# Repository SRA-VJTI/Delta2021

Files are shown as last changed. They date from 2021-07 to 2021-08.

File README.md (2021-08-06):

# Delta-Resources-2021

---

## Table of Contents
- [Introduction](#introduction)
- [Proposal](#proposal)
- [Design](#design)
- [Journey](#journey)
- [Algorithms](#algorithms)
- [Software used](#software-used)
- [Competition Snaps](#competition-snaps)
- [Products used](#products-used)
- [Results](#results)
- [Prizes and Achievements](#prizes-and-achievements)
- [Team - DNS](#team---dns)
- [Mentors](#mentors)
- [Organizations](#organizations)
- [References](#references)

## Introduction
 
 - The **7th Delta International Smart & Green Manufacturing Contest** is themed "Seeking Smart IIoT Talents" and offered three tracks: "Innovative Machines", "Smart Factory", or "Better Future Living".
 - Our **Team DNS** took up the **Smart Factory track**, we were expected to present realistic solutions or approaches with digitalization, IIoT, and big data management for optimized production processes, high-efficiency management & production, enhanced safety & reliability, quality improvement, energy savings, predictive diagnosis and maintenance, and green solutions.
 - The Contest is **hosted by** the Chinese Association of Automation **(CAA)** and sponsored by the Chinese Association of Automation, and the Industry and Information Industry Vocational Education Teaching Steering Committee **under the Ministry of Education**. It is an innovative technology competition for automation, smart manufacturing solutions and green technology applications organized by the **Delta Group**.

## Proposal
- Our Team DNS proposed the Pick Sort Place Bot
- So after researching on some trends and practices currently followed in the packaging industry, we noticed that there were shortcomings in case of:
  * Variable sized item packaging
  * Location based item packaging
  * Custom subscription box based packaging
- And we took to solving that with our [proposed idea](https://github.com/SRA-VJTI/Delta2021/blob/main/docs/proposal/delta2021090_PSP_Bot_Proposal.pdf)

## Design
The complete mechanical structure is designed in **Solidworks2021**. Dimensions, assemblies and sub-parts were finalised considering the following:
* Material Strength
* Stress, material and displacement analysis
* Material Availability

### Manufactured Product
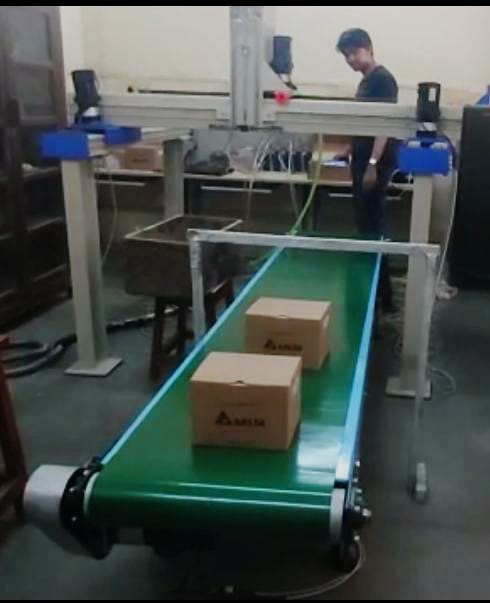
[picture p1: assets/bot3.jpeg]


### Raw Frame 
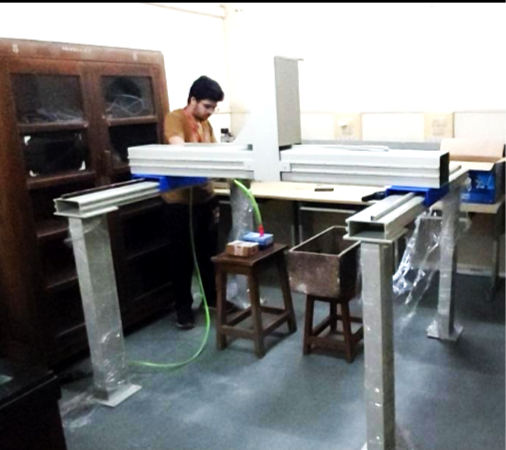
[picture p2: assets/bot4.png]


### Structure with Conveyor Setup
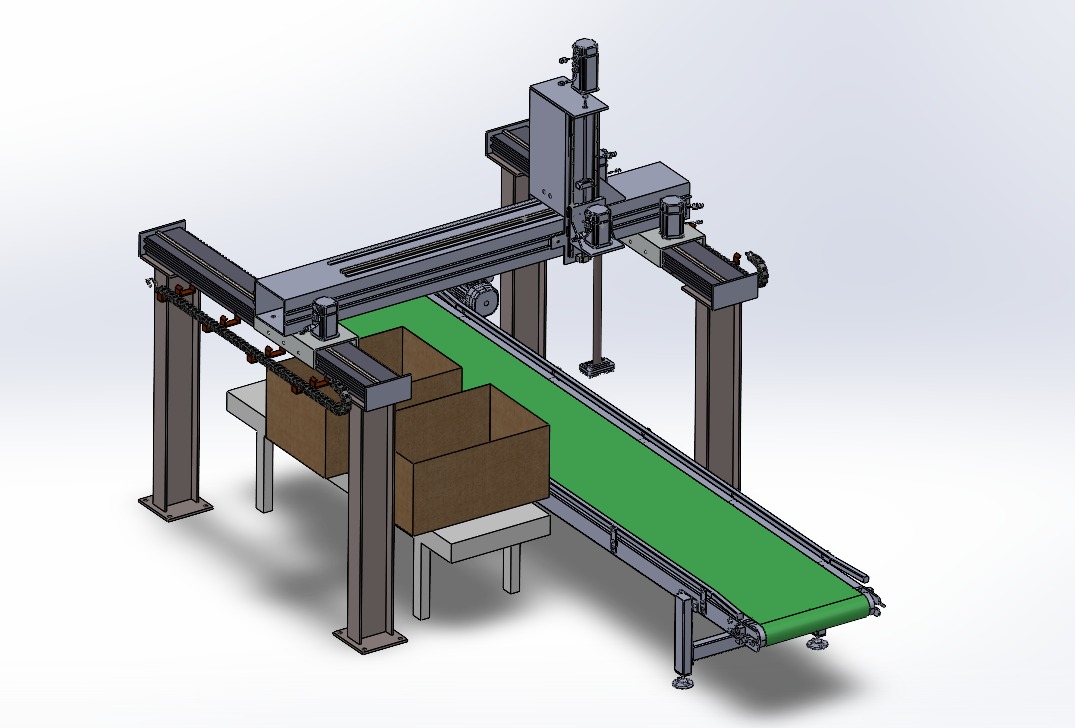
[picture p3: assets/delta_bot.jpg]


### XYZ Gantry Frame
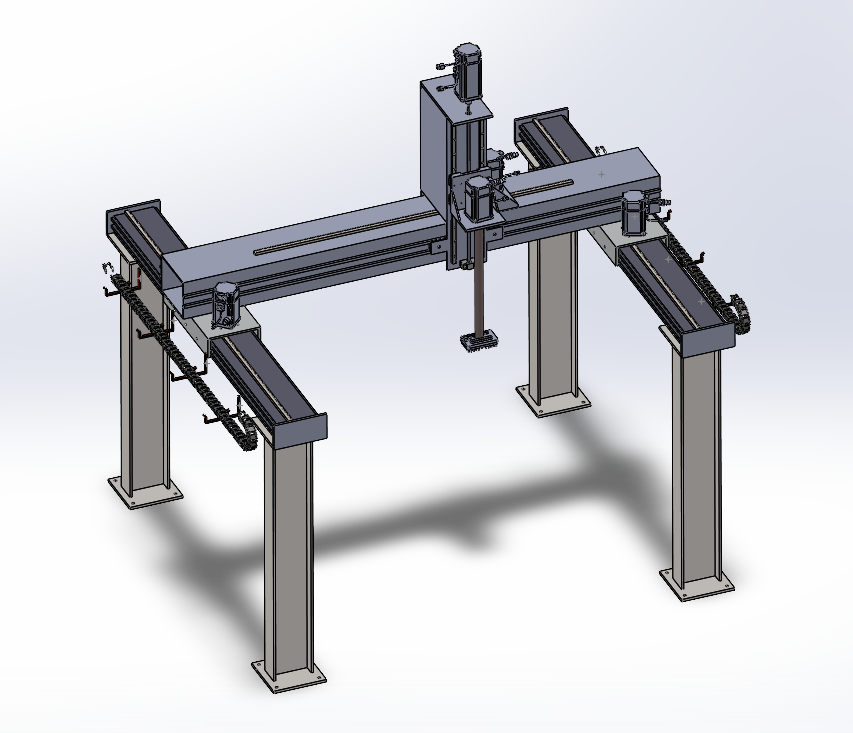
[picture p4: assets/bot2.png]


## Journey


## Algorithms
We are trying to implement a 3D binary packaging algorithm to reduce wastage of space ensuring efficient packaging of input items in output containers.
<table>
<tr>                   
<td>

### Loose Input Items
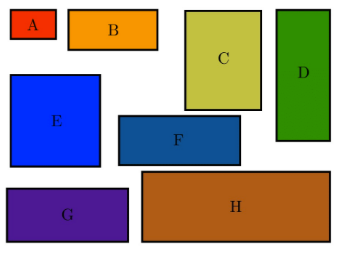
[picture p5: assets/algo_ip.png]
</tc>
<td>

### Close Packaging
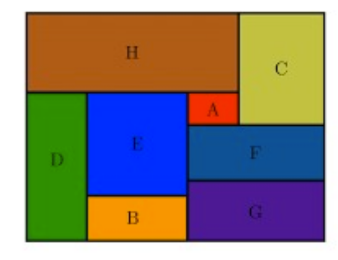
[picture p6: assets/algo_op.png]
</td>
</tr>
<tr>

### 3D Packaging
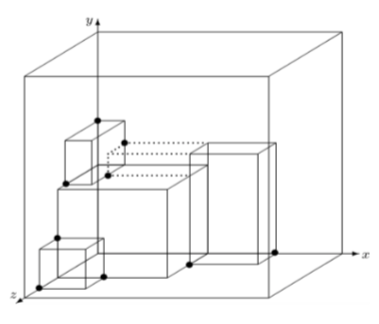
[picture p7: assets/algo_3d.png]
</tr>
</table>

## Software used
1. **Delta's CANopen** - To program the PLC Motion Controller. Currently, **ladder** language was used for programming.
2. **DOPsoft** - To design and program the Human Machine Interface - HMI.

## Competition Snaps
### X Y Axis Motion


## Products Used
### 1. PLC - Motion Controller 
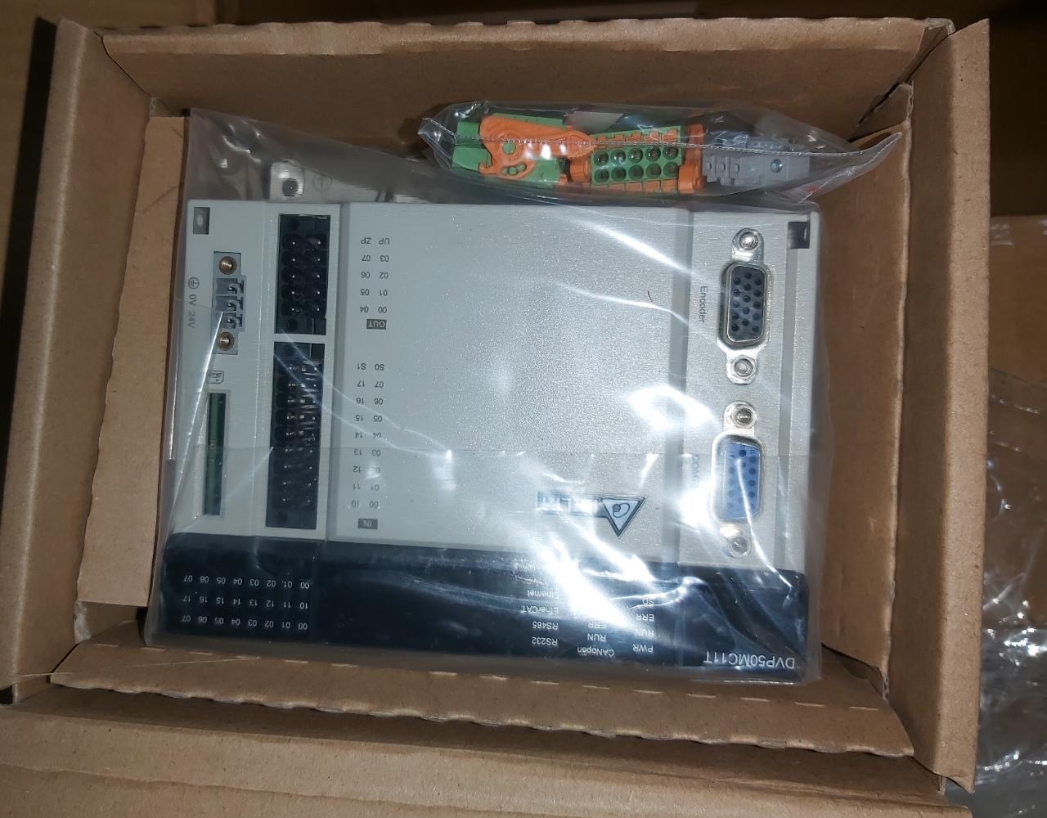
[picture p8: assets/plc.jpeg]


### 2. Conveyor Belt System
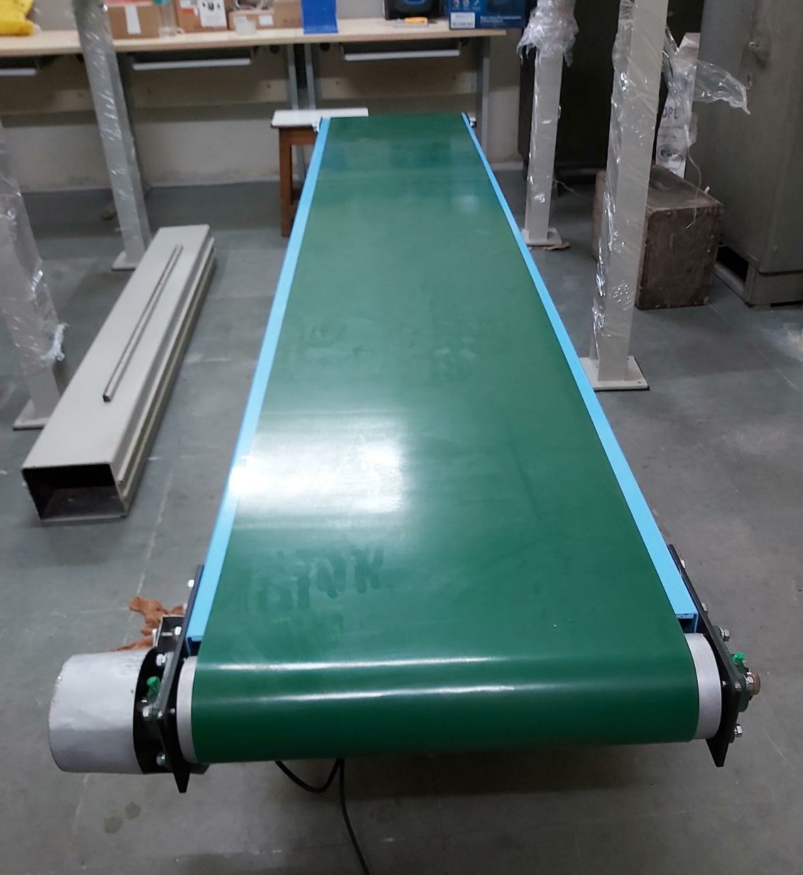
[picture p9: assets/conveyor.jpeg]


### 3. Machine Vision Lens and System
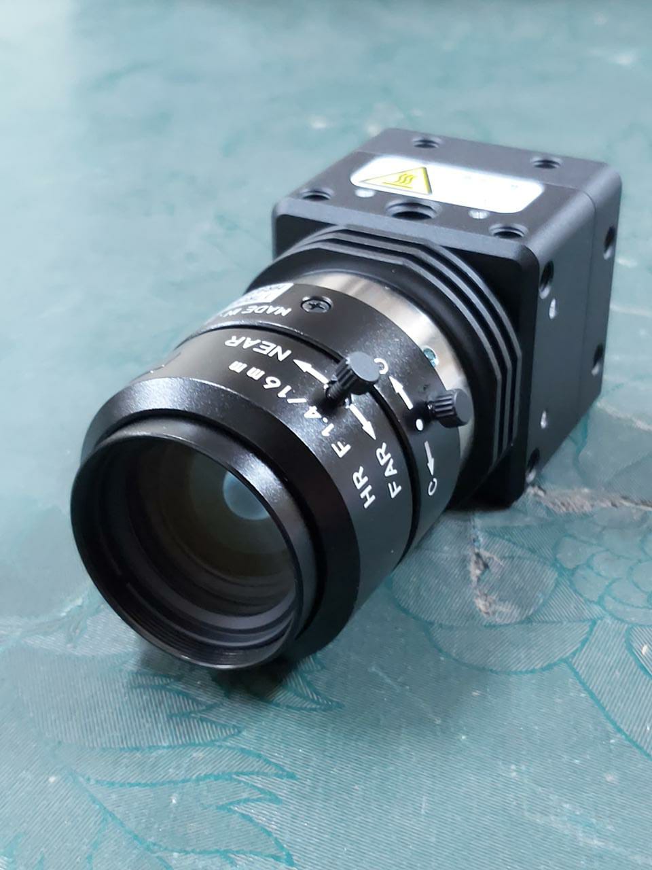
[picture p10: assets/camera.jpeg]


### 4. AC Servo Motor
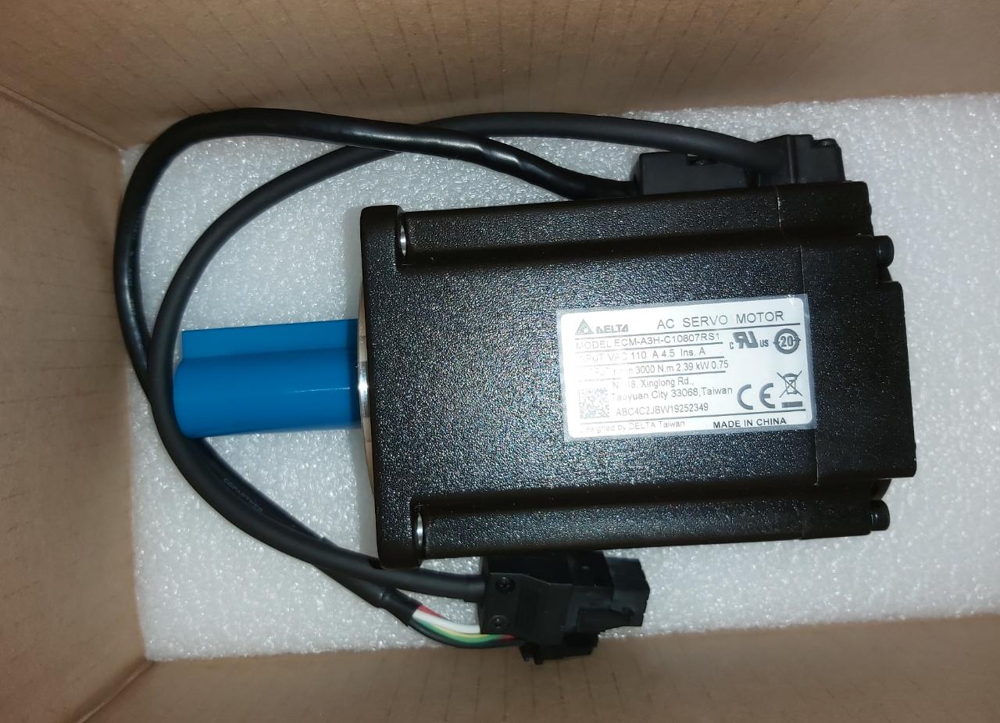
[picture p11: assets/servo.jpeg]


### 5. Servo Drives
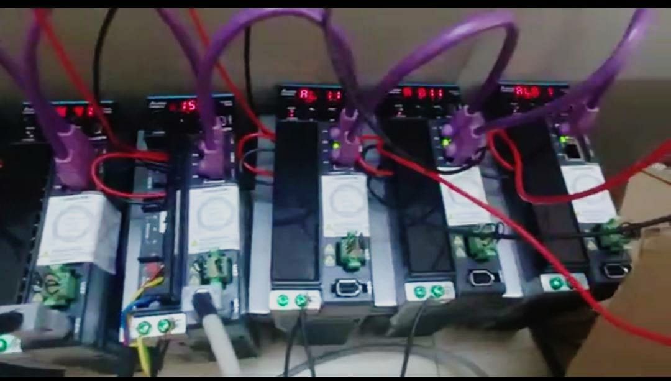
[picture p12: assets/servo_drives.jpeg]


### 6. IIoT Router
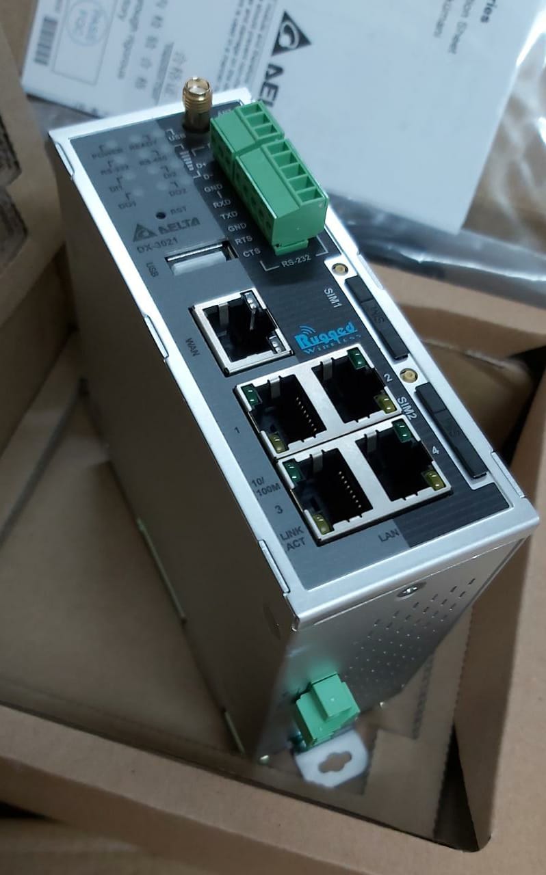
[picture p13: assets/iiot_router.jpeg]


### 7. HMI - Human Machine Interface
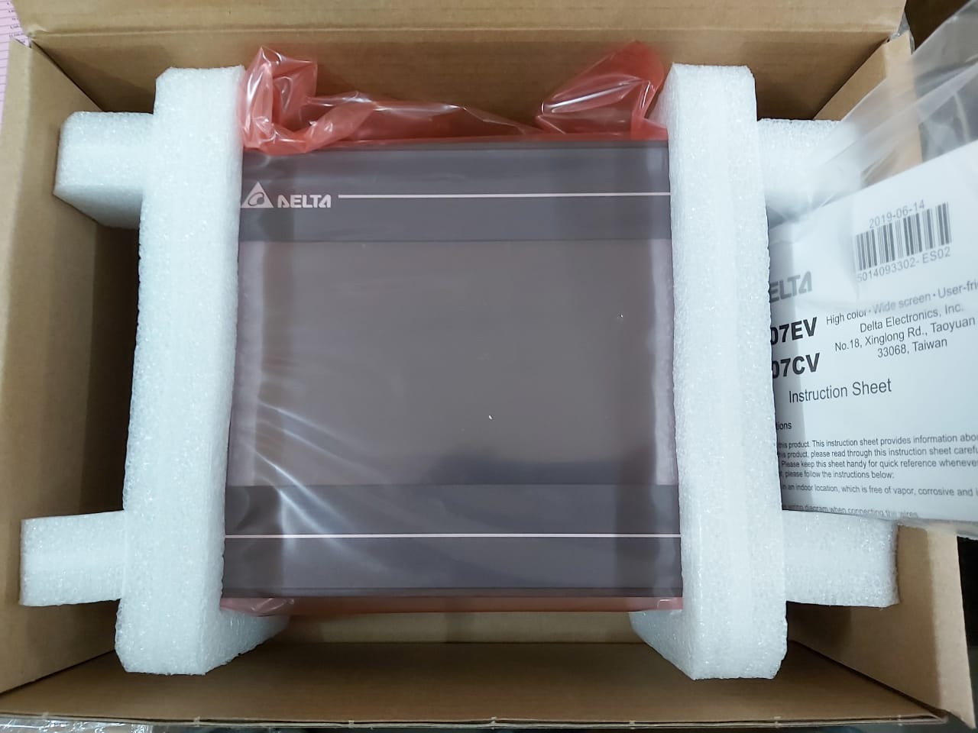
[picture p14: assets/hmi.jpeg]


### 8. Laser Displacement Sensor
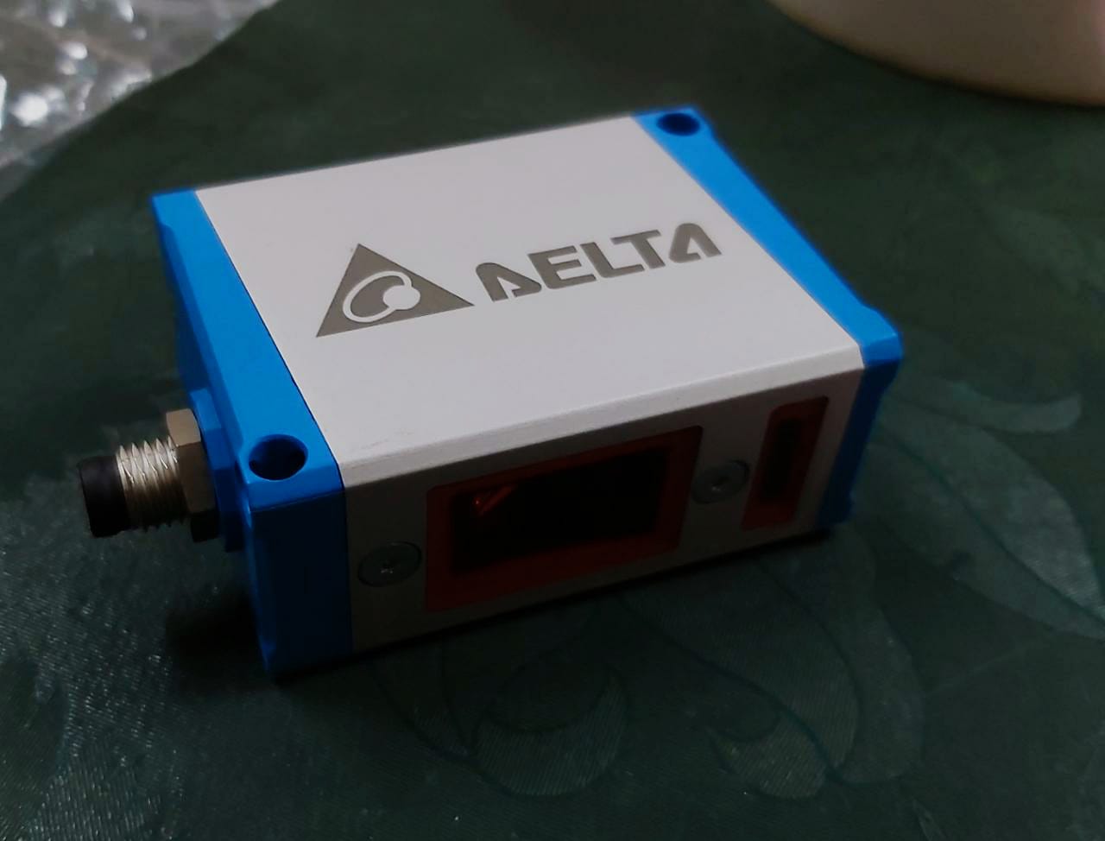
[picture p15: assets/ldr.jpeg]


## Results
- Representing India, Team DNS and VJTI bagged a rank under **Top 40** globally winning the **Second Prize** category.
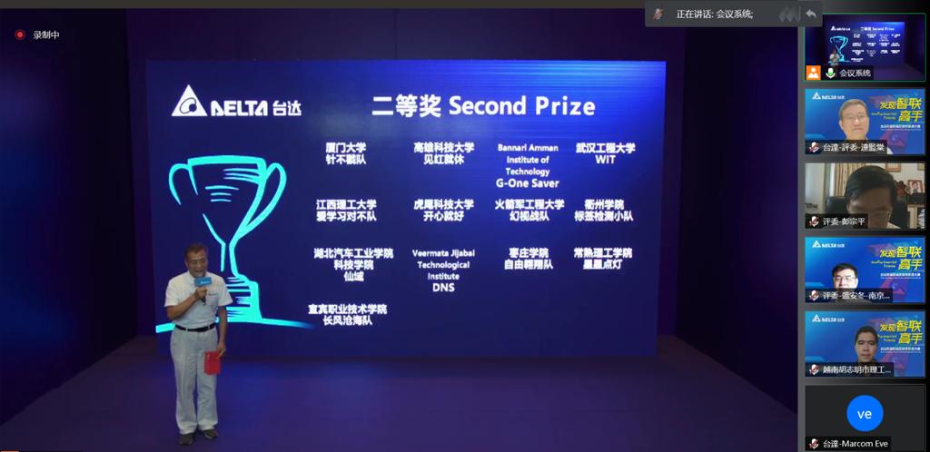
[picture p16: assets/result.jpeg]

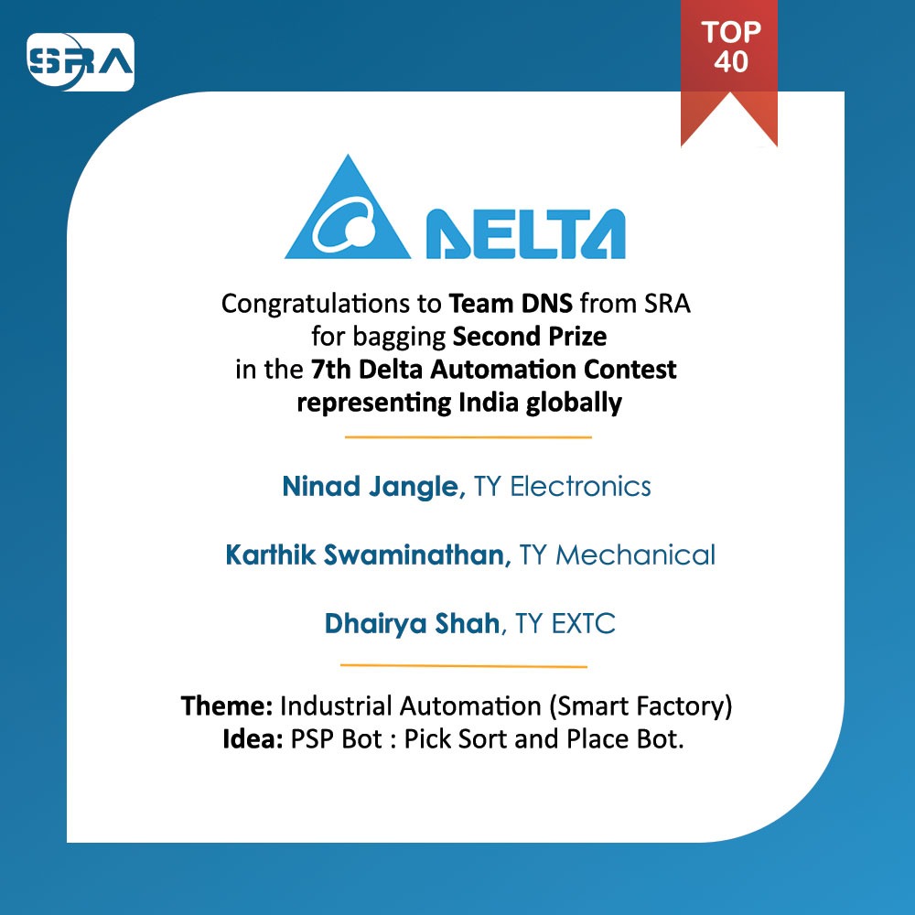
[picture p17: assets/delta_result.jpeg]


## Prizes and Achievements
1. Trophy Shield - Second Prize category
2. Delta's Industrial Automation Products Worth Rs 16.8 lakhs free of cost
3. 3000 RMB Cash Prize

## Team - DNS
- [Dhairya Shah](https://github.com/dhairyashah1/)
- [Karthik Swaminathan](https://github.com/kart1802/)
- [Ninad Jangle](https://github.com/ninja3011/)

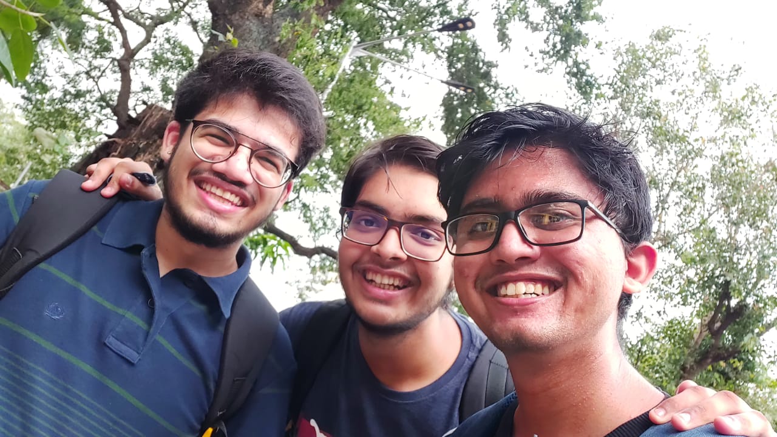
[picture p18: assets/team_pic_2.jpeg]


## Mentors
- [Dr. Faruk Kazi](https://www.linkedin.com/in/dr-faruk-kazi-vjti/?originalSubdomain=in)
- [Mr. Alister D'Silva](https://www.linkedin.com/in/alister-dsilva/)
- [Omkar Bhilare](https://www.linkedin.com/in/omkar-bhilare-985aa2180/)

## Organizations
- [VJTI](https://www.vjti.ac.in/)
- [SRA-VJTI](https://sravjti.in/)
- [COE-VJTI](https://www.vjti.ac.in/images/coe-cnds/project/index.html)
- [Absolute Motion Pvt Ltd](https://absolutemotion.in/)

## References

1. [Introductory Video](https://youtu.be/Td_gTH8elXg)
2. [Journey and Demo Video](https://youtu.be/JBdjbeT3EMY)
3. [Demo Video](https://youtu.be/Td_gTH8elXg)
4. [PSP BOT Presentation](https://github.com/SRA-VJTI/Delta2021/blob/main/docs/presentation/presentation.pdf)

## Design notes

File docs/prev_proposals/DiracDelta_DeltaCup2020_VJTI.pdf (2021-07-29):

## Seeking Smart Manufacturing Talents

## The 5th Delta Advanced Automation Contest

Project Proposal
Team Number:
Proposal Name | AARobot (Autonomous Agricultural Robot)
Team Name | Dirac Delta | University/ Affiliation | Veermata Jijabai Technological Institute, Mumbai, India
Team Leader | Name | Omkar Sargar | Department | B.Tech Electronics Engineering
| Mobile | 9969398226 | Post Code | 410206
| Email | omkarsargar01@gmail.com
| Address(City,State, Country) | 01, Nirman Sagar CHS, Thana Naka, Panvel, Maharashtra, India
Member Names | Lukesh Ankamwar B.Tech Electronics Engineering lukeshankamwar2103@gmail.com Omkar Bhilare B.Tech Electronics Engineering ombhilare999@gmail.com

## Team Building:

### 1. Mr. Omkar Shivaji Sargar (Age 19)

Bachelor of Technology Electronics Engineering, Veermata Jijabai Technological Institute (VJTI)
https://github.com/OSSome01
- Bachelor of Technology Electronics Engineering, 7.4 CGPA as on III semester (08/2018 to present) Maharashtra State Board Higher Secondary Certificate (Science), 78.45%

(08/2016 to 05/2018) All India Secondary Certificate Examination (10th Standard), 10/10 CGPA

(04/2015 to 04/2016)

Role: Computer Vision, Machine Learning and Programming.

Skills and Specialization: Hardware: NodeMCU, ESP-32, Rasberry Pi, Azure Sphere. Software Program: Eagle PCB, Multisim, ESP-IDF, Arduino IDE. Programming Languages: C, C++, Python, Robot Operating System (ROS),

Ladder Logic Programming, Data Structures and Algorithms. Key Technical Skills: Robotics, Simultaneous Localization And Mapping (SLAM),

Machine Learning, Computer Vision, Image Processing, Programming.

Specialization: Robotics and Automation.

Achievements: First prize: Labyrinth 2019 (Autonomous maze solving robot), VJTI. Third Prize: Autobot Challenge 2018, VJTI.

Projects: Smart Light: An IoT based project developed using ESP32, which optimizes the

brightness of an LED according to the ambient lighting conditions. Maze Solver: A robot designed to map any random maze in dry run and solve the maze

in the final run by following the shortest route possible. Object Detection: Software that uses a Kinect 360 to recognize a particular object in a

surrounding with the help of several digital image processing algorithms and provide the user with information like its distance from the camera, its dimensions and surface area. Self Balancing Robot based on PID controller: An Autonomous Robot that follows a

line and balances itself on only two wheels using PID control system and Embedded Electronics.

- 3-DOF Robotic Manipulator: A manipulator with 3 Degree of Freedom (DOF), interfaced with Robot Operating System (ROS) & implemented using ESP32. Simultaneous Localization And Mapping (SLAM): Simultaneous Automation

and Mapping using Intel Real Sense D435.

### 2. Mr. Omkar Ananda Bhilare (Age 19)

Bachelor of Technology Electronics Engineering, VeermataJijabai Technological Institute (VJTI)
https://www.linkedin.com/in/omkar-bhilare-985aa2180/ Bachelor of Technology Electronics Engineering, 9.73 CGPA as on III semester

(08/2018 to present) All India Secondary Certificate Examination(Diploma in Electronics), 97.15 %

(08/2016 to 05/2018) All India Secondary Certificate Examination (10th Standard), 95.2 % (04/2015

to 04/2016)

Role: Electronics and Electrical system design and programming.

Skills: Hardware: NodeMCU, Esp32, Atmel AVR(16,32,328P), Rasberry Pi. Software Program: MATLAB, Eagle PCB, Altium, Keil MDK, Multisim and

proteus Programming Languages: Embedded C, Python, C.

Specialization: Embedded System and Automation.

Achievements: State Rank 1 in electronics in diploma. Participated in various project presentation competition. Third Prize: Technical Paper Presentation, VJTI

Projects: Universal Integrated Circuit: The digital trainer kit which can clone multiple IC's Automated Seed Sower: Customizable robot which can sow seeds according to

user's need Line following robot. Home automation using NodeMCU Air quality monitoring system

### 3. Lukesh Narsingh Ankamwar (Age 20)

Bachelor of Technology Electronics Engineering, Veermata Jijabai Technological Institute (VJTI)
LinkedIn:-https://www.linkedin.com/in/lukesh-ankamwar-212566173/
- Bachelor of Technology Electronics Engineering, 8.13 CGPA as on III semester (08/2018 to present) Maharashtra State Board ,(12thStandard),83.33 % All India Secondary Certificate Examination (10th Standard), 90.4 %

Role: Mechanical system design and programming.

Skills: Hardware: NodeMCU, Esp32, Atmel AVR (16,32,328P), Rasberry Pi. Software Program: Solidworks, Crio, Ansys, MATLAB, Eagle PCB, Altium, Keil

MDK, Multisim and proteus Programming Languages: Python, C and C++.

Specialization: Mechanical Design and Analysis.

Achievements: First prize: Labyrinth 2019 (Autonomous maze solving robot), VJTI. Third Prize: Autobot Challenge 2018, VJTI.

Projects: Maze Solver: A robot designed to map any random maze in dry run and solve the maze

in the final run by following the shortest route possible. Object Detection: Software that uses a Kinect 360 to recognize a particular object in a

surrounding with the help of several digital image processing algorithms and provide the user with information like its distance from the camera, its dimensions and surface area. Self Balancing Robot based on PID controller: An Autonomous Robot that follows a

line and balances itself on only two wheels using PID control system and Embedded Electronics. 3-DOF Robotic Manipulator: A manipulator with 3 Degree of Freedom (DOF),

interfaced with Robot Operating System (ROS) & implemented using ESP32.

## Introduction:

Problem Insight:

Employment in the agricultural industry fell by 9 million from 2011 to 2018, contrasting to the 93 million increase in population in the same period. The newer generations are not interested in agriculture and hence the ratio of demand to supply is very high. Thus introducing automation and robotics in agriculture is a better method to improve overall agricultural produce and reduce labor requirements. There are very limited automatic agricultural robotic systems available in India but they are not feasible and are usually oriented towards harvesting, cleaning and packaging agricultural produce. The damage to agricultural crops due to pests account for 13.6% annual loss globally (which accounts for around 18 billion dollars). Similarly weeds amount to 8.8% annual loss globally. Additionally a loss of 861.8 million is incurred due to over usage of fertilizers in India. It would be a huge boon for the Indian Agricultural Industry if these losses can be minimized with the help of Automatic Agricultural Robots.
Project Idea:

After analysis the current situation of Automation in Agriculture we have come up with a innovative idea to design a solar powered agricultural robot which can do various tasks like: pest removal, weed removal, spraying fertilizer, helping in cattle farming, and generating electricity to power basic appliances in the farm. The robot will have two operating modes: automatic and semi-automatic. The robot will help to reduce the wastage of time and other resources needed in the above mentioned tasks. AARobot will also help to analyze the crops by sending data to a cloud server where analysis will be done on the data and the feedback will be provided to the farmers.
Using the concepts of Machine Learning, Computer Vision, Mobile Robotics we aim to build AARobot. Traditionally the main area of application of Automatic Agriculture Robots is at the harvesting stage. These robots are usually designed to do only a specific set of tasks, which makes them even more impractical for Indian farmers. We are aiming to maximize the produce by dealing with the losses incurred due to pests, weeds and overuse of fertilizers. Also we are designing a robot which can do varied tasks like helping in cattle farming, generating electricity for basic farm needs, and thus increasing its value for money.

## Objectives:

### 1. Crop Detection 2. Pest detection and removal 3. Weed detection and removal 4. Optimizing the process of spraying fertilizer 5. Analysis of data provided by AARobot. Sending all the data collected (Number of

crops, number of crops infected by pests, number of weeds detected, area of farm where maximum number of pests and weeds were detected, etc.) to a cloud and perform analysis on this data and give appropriate feedback to the farmer.
6. Designing a simple but effective system on the AARobot to help with cattle farming.
7. Charging a battery which can then be used for basic powering electrical appliances.

## Applications:

Crop Detection: We are using Machine Learning and Computer Vision algorithms to detect crops in the field. In our case we are detecting cabbage a common vegetable grown and consumed in India. After a plant is detected the robot will perform all the tests and the details of the plant will be uploaded on the cloud.

Case 1:
The damage caused to agricultural produce due to pests is very high. Traditional methods like using bright sticky pads are quite effective to counter flying pests; however there are no good solutions to counter bugs and ground pests. The only solution for bugs is the use of pesticides, but it leads to pollution and may also damage the crops if not used in proper quantities.
Solution:
Pest Detection and Removal: We are using Computer Vision algorithms to detect pests on cabbage plants. We are proposing to use a thermal camera which can be used to detect pests accurately. After a pest is detected a pest removal tool will help to suck off the pest from the plant. The detailed working of the pest removal tool is specified in the upcoming sections.

Case 2:
Traditionally weeds are removed manually by hand picking or by the use of weedicides. The first method impractical as it is very time consuming and is also not feasible as labor costs are very high. The second method leads to pollution and may destroy the crops if not used in proper quantities.
Solution:
Weed Detection and Removal: This will be similar to crop detection where Machine Learning and Computer Vision algorithms will be used. After a weed is detected a weed removal tool will act to remove the weed. The detailed working of the weed removal tool is specified in the upcoming sections.

Case 3:
Traditional methods of spraying fertilizer include manually spraying fertilizer using a pump like device. Manual spraying of fertilizers often lead to improper dosage to plants which may destroy the crops. It also leads to wastage of fertilizers. Manual spraying of fertilizers is also harmful for humans if proper precautions and safety measures are not followed. Solution:
Spraying Fertilizer: When a crop is detected the robot will calculate the midpoint of the crop and a spraying tool will spray the fertilizer at the exact location calculated, thus reducing the amount of fertilizer used and hence optimizing the process.

Case 4:
Usually in cattle farming when the cattle are to be taken out for grazing humans are needed to keep them in check and guide them to the grazing grounds.
Solution:
System for Cattle Farming: This is a simple add-on feature wherein a speaker can be mounted on the robot which will play the cattle owner’s voice in a loop to attract the cattle towards it. Thus it can be used to direct the cattle towards grazing grounds. It will help reduce the involvement of humans as the robot can be controlled remotely.

Case 5:
In India it is a common practice that in every farm there is a small room or house which is made to keep all the necessary tools and equipment (this room is equipped with basic electrical appliances like tube-light, fan, etc.). Also there are bore wells which are used as a primary water source for agriculture in many parts of India. Many regions in India don’t have electricity supply which makes it difficult for the farmers to use bore wells.
Solution:
Battery Charging: A additional feature which can be added is that AARobot can be used to charge a Battery which can then be used to power basic electrical appliances in the farm.

Use of IIoT: The contribution of agriculture plays an important role in the economic growth of

India. In India, more than 60% of peoples depend upon agriculture. This 60 % of people produce food for the country. Recently, the number of farmers in India decreasing day by day. The agriculture results depend up on the various controlled and uncontrolled factors like sudden change in climatic conditions; high and low rain fall and also the timing of the rain, storms and heat waves, and effects of cold, etc. For these conditions, traditional farming techniques are not appropriate. To minimize these effects and increase the productivity of agriculture,

automation and IoT techniques are required.

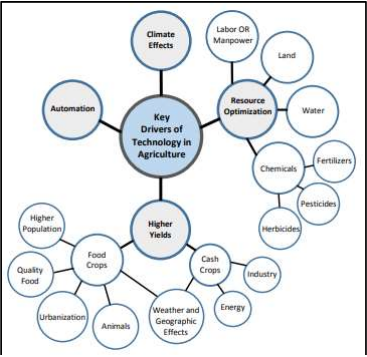
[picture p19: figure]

- In this project we have integrated internet of things such that the overall efficiency and usability Increases exponentially. We are focusing on automation of weed and pest removal and also, on resource optimization like chemicals, pesticides etc.

The use of IIOT in this project explained in following steps:

### 1. Detection of plant and its center:

- Before proceeding further for pest and weed removal we needed to detect plants, we have detected plant using OpenCV (computer vision). The example of detection of plant given below:

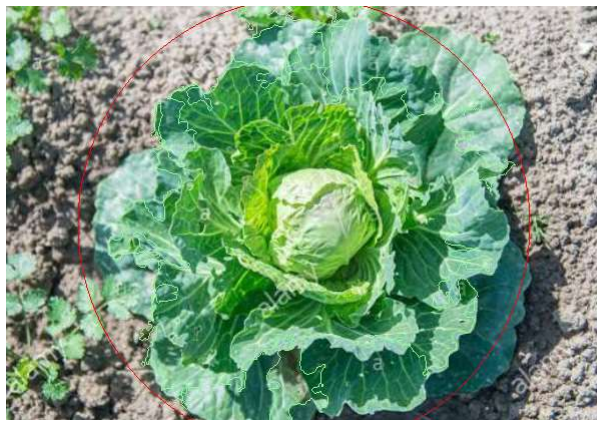
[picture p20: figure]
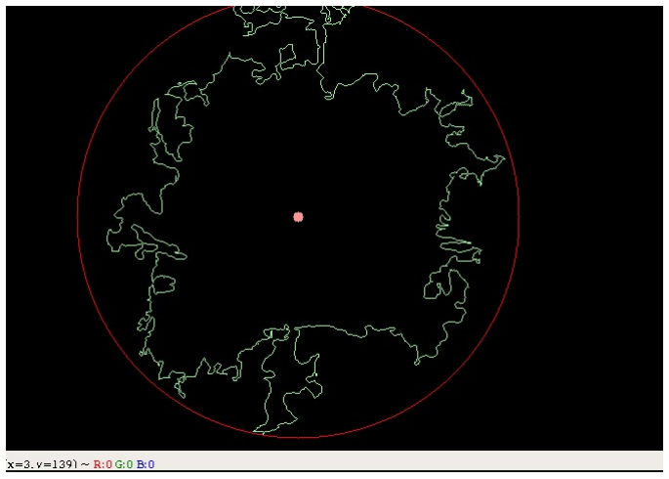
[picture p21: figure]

- By using OpenCV we were
which we can fertilize the plant, and if we provide the data set of same plant with infection.
- Then we can also detect
- And by using same technique we can also detect pest in plants and furth remove it using vacuum

### 2. Availability of data on cloud:

- After obtaining data from
further analyzing of obtained dat

CV we were able detect the center of the plant by using which we can fertilize the plant, and if we provide the data set of same

Infection in plant.
And by using same technique we can also detect pest in plants and furth vacuum

OpenCV program it is send to cloud for a

er

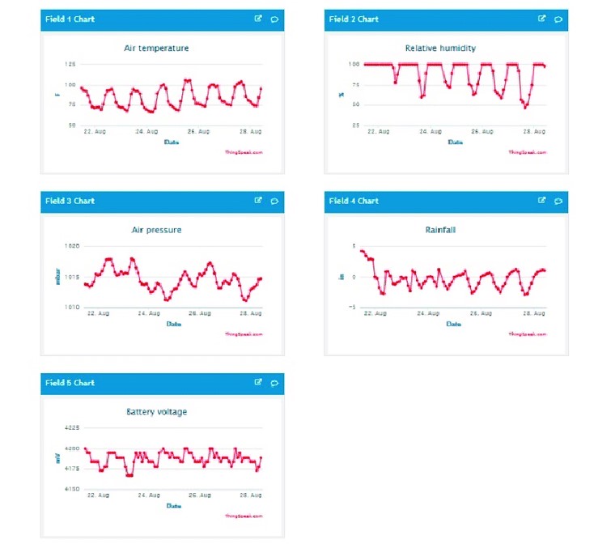
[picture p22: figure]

- We can monitor data on cloud and graphs like above can be made.
- In specific by plotting graph of pests captured w.r.t to its position in the field we can monitor the specific area where density of pests is more so one can take appropriate steps to reduce its adverse effects.

Thus, by using internet of things we can increase the productivity of agriculture and overall profit will also be increased because of IOT.

## Robot Design:

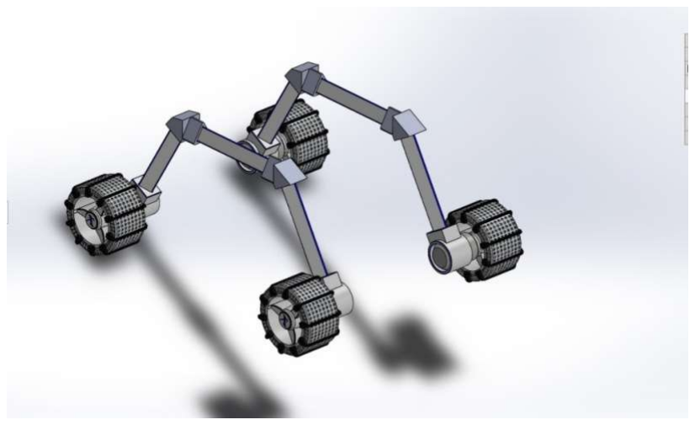
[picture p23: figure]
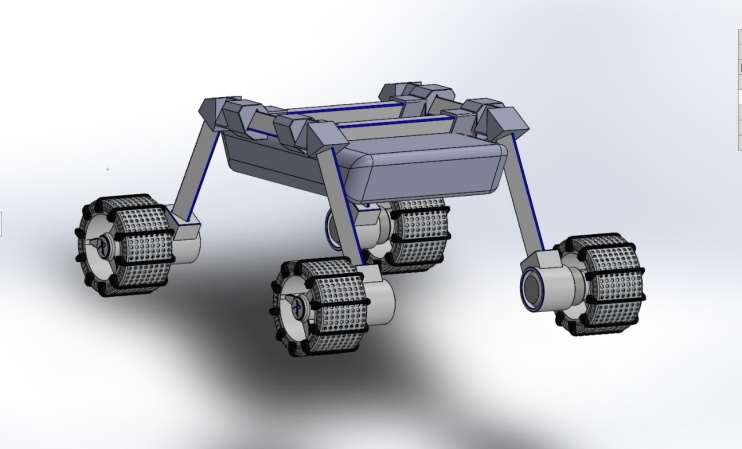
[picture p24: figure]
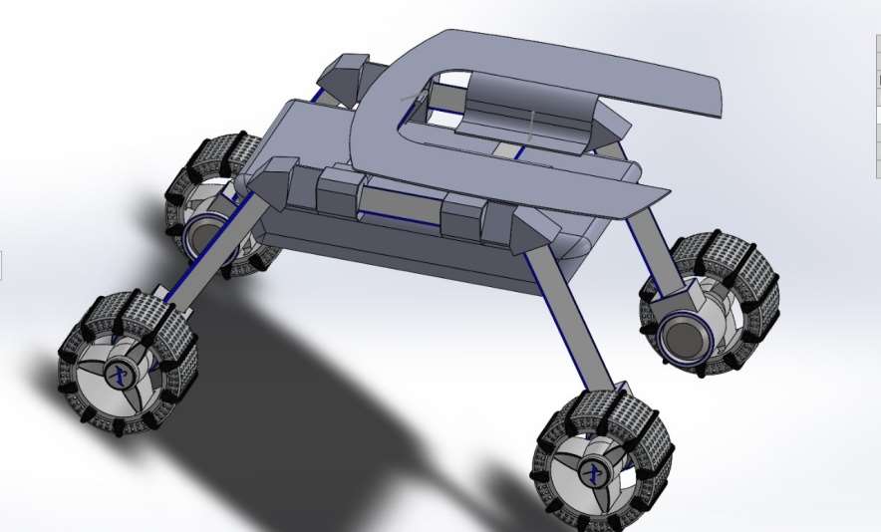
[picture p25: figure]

## Working:

Motion Control:

### 1. In the base of this project we are going to use two delta servo motor whic

coupled with the two rear wheels and front two wheels are used as dummy wheels.

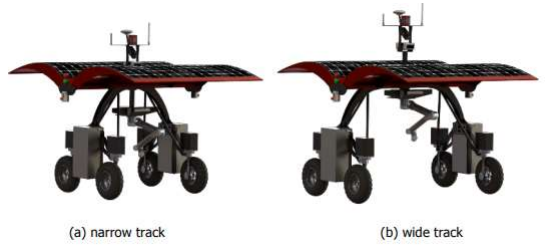
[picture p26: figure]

### 2. In this project, we are keeping wheel configuration dynamic that is the distance

between two side wheels can be customizable according to user input on HMI panel. T will be achieved by using two delta servo motors directly coupled to two lead screw.

3. In our project motion control system is going to have high accuracy, high speed, insignificant or no overshoot and robustness. To achieve this we are going to use a P controller which will be mathematical model of a motor based on classical root approach.

two delta servo motors directly coupled to two lead screw.

h are gear

his

ID
-locus

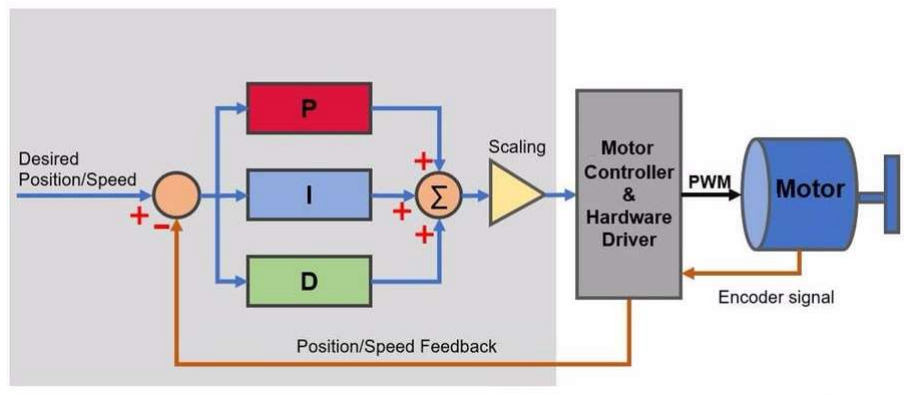
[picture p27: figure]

Tool Control:

In this Project we are using Three Main tools which are stated as below:

### 1. Vacuum for pest removal 2. Spray gun to spray fertilizers 3. Weed Removal tool for removing weed

1. Vacuum: A vacuum gun will be used to suck pests off the plants.
2. Spray gun: A pump motor is used to spray fertilizers on the farm land. Here we are using universal joint to move spray gun. The reason for using universal joint is to access every point in the frame.

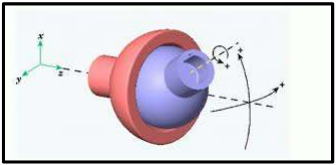
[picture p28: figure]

Working Video Link: https://youtu.be/Sef_fJh3OgQ

### 3. Weed Removal tool:

This robot can be also used to remove weeds from the surface of the field. To remove weed we have designed our own weed removal tool according to our need.

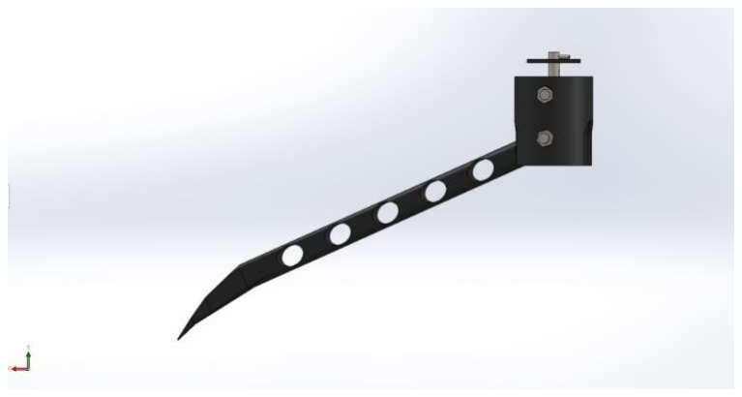
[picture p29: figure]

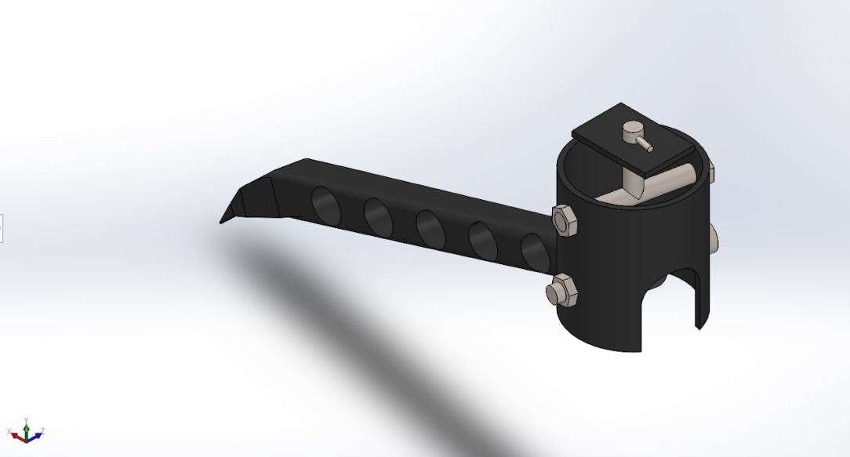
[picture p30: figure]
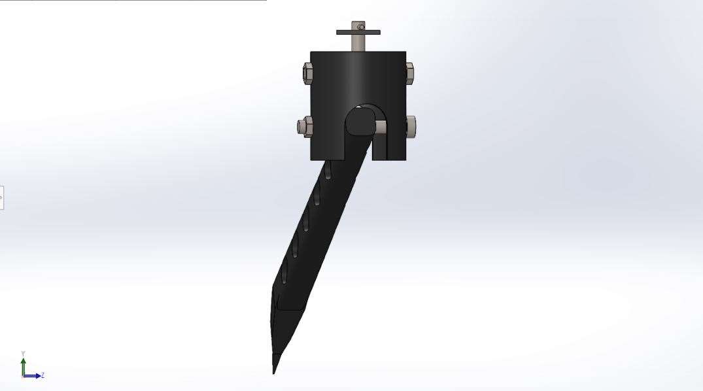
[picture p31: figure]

Working Video Link: https://youtu.be/WgTvQdC92Rchttps://youtu.be/4lKjg0JsSTg

Robot’s Work Space: Robot can move anywhere in the normal farm. Robot can move in muddy and rocky surface Cannot move on extremely uneven terrain.

Uncertain Error Handling: In any uncertain situation the robot will be stop working and battery will be open

Circuited so electrical safety is maintained. Emergency Alarm will be switched on and emergency light will be displayed HMI panel will show the information which will help to debug these uncertain errors.

## Innovative Planning and Value:

### 1. AARobot is a unique robot which will strive to increase the efficiency of tthe

agricultural industry. It is one of a kind robot which will help in such aspects of agriculture which are traditionally ignored by the other robots available in the industry.

### 2. The main idea is to make a multi-purpose automatic robot which can perform multiple

tasks and hence provide good value for money.

### 3. Using concepts like Machine Learning, Computer Vision and Mobile Robotics

AARobot will boost the agricultural industry and will help reduce human interference in agriculture.

## Cost Analysis, Feasibility and Reasonability:

As we are using all parts according to the industrial standards, we are having very cost-effective structure. AARobot is a multi-purpose robot and hence improves the value for money. If we compare the losses incurred by farmers due to the various issues which AARobot is trying to solve to the cost of the robot then we can say that its cost is well justified.

## Component Specification and Bill of Materials:

Sr | Product Name | Delta Product Code | Quantity | Description
1 | Wireless Module | DVW-W02W2-E2 | 2 | To connect with internet
2 | Servo Drivers | ASDA2ServoDrives | 4 | To drive all Axes motors
3 | Servo Motors with encoders | ASDA20721U | 4 | To drive all Axes motors
4 Planetary | Gearbox | PS Series | 2 | To change torque based on requirement for Constant speed motor.
5 | PLC | DVP28SV11R2 | 1 | Main controller which accept the input through HMI and cloud server and do control according to ladder logic.
6 | HMI | DOP-107WV | 1 | To observe the status of the robot on the field and to control it

7 AC-DC Power | Module | AB60S2400A | 1 | For power supply to PLC (24V)
8 Analog I/O | Modules | AH04AD-5A | 3
9 | Vision Sensor | VIS100 Series | 2 | For object detection on plants and positioning of robot

OTHER PRODUCTS

10 | Microprocessor | Raspberry Pi | 2 | For any alien object detection on plant and sensor data acquisition
11 | Wheels | Third Party | 4 | For moving the robot on field
12 BLDC Blower | Fan | Third Party | 2 | For cooling Drives
13 Power | Supply(5V) | Third Party | 2 | For powering microcontrollers and other peripherals
14 | Wire | Third Party | Multiple | Wiring
15 | Wire Connector | Third Party | Multiple | Wiring

16 | Microcontroller | Arduino UNO | 1 | For sensor data acquisition in BOTs
17 Ethernet Shield | for Arduino | Third Party | 1 | For IoT Application
18 Ball | Bearings | Third Party | Multiple | Miscellaneous
19 Linear | Bearings | Third Party | Multiple | Miscellaneous
20 | Solar Panels | Third Party | 2 | For charging the battery
21 | Nuts and Bots | Third Party | Multiple | Miscellaneous
22 Spacers and | Washers | Third Party | Multiple | Miscellaneous
23 | Power inverter | Third Party | 1 | For Solar Panel
24 | Kill Switch | Third Party | 1 | For Stopping all applications
25 | Sprinkler | Third Party | 2 | For sprinkling fertilisers
26 | Storage Tank | Third Party | 1 | For storing seeds/fertiliser
27 | Vacuum Pump | Third Party | 1
28 | DC Servos | Third Party | 5 | For use in various tools

## Future Scope:

1. It can be further used in Harvest management.
2. It can be also used for Field Mapping.
3. It can be used for Soil Management.
4. It can be an important part of a greener future for mass scale farming.
5. By bringing Artificial Intelligence and around the clock activity, the robots will help optimize the yield of farm far beyond what could humanly be possible.

## Summary:

The AARobot is thus a feasible multi-purpose automatic agricultural robot which can help boost the agricultural industry in India.

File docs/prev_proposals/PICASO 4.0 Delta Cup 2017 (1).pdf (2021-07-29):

## Seeking Smart Machine Talents

## The 4th Delta Advanced Automation Contest

## PROJECT PROPOSAL

TEAM Code: delta2017127 | TEAM ID: 435
Proposal Name | PICASO 4.0
Name Team | PICASO | University | Lovely Professional University, Punjab, India
Team Leader | Name | Mr. Arnab Kumar Das | Department | Bachelor of Technology Electronics and Communication
| Mobile | +91 9501991556 | Post Code | 713101
| Email | arnab.das.bwn@gmail.com
| Address | 56, Goal Ghar Saradapally, Near Goal Ghar Primary School, Burdwan, PIN – 713101, West Bengal, India
Member Names | Mr. Nikhil Goyal, B.Tech Electronics and Communication Engineering, nikhilgoyal2311@gmail.com , +91 9915727112 Mr. Veluguri Vinod, B.Tech Mechanical Engineering, vinod.veluguri@gmail.com , +91 9872386996

Team Building

### 1. Mr. Arnab Kumar Das, Age 23

Bachelor of Technology Electronics and Communication Engineering, Lovely Professional University
https://www.linkedin.com/in/arnabdasbwn/
Specialization: Embedded System and Robotics

ROAL: Electronics and Electrical System Design and Programming.

- Bachelor of Technology (Honors) Electronics and Communication Engineering, 9.0 CGPA as on VII Semester (08/2013 to Present)
- Indian School Certificate (12th Standard), 90.0% Aggregate Result (04/2011 to 04/2013)
- Indian Certificate Secondary Education (10th Standard), 87.8% Aggregate Result (04/2011)
- Hardware: Atmel AVR (16/32/328p), Raspberry Pi, Arduino, Microchip PIC, ARM7
- Software Program: AVR Atmel Studio, LabVIEW, Cadence, Eagle PCB, MATLAB, Keil MDK for ARM
- Programming Languages: Embedded C, Verilog, Embedded C++, Virtual Instrumentation, C, C++
- First Prize - Line Follower Robot Competition, Fluxus’16, IIT Indore, 2016
- Participated in Remote Control Ship and Aeroplane Competition, Cognizance’16, IIT Roorkee, 2016
- First Prize - Remote Control Car Race, Lovely Professional University, 2015
- Participated in E–Bike Manufacturing and Racing Challenge, Imperial Society of Innovative Engineers, 2015
- Participated in Hybrid Go-Kart Making Challenge, Imperial Society of Innovative Engineers, 2015
- Participated in World Skill India in Electronics, World Skill International Competition, 2015

### 2. Nikhil Goyal, Age 21

Bachelor of Tech Electronics and Communication Engineering, Lovely Professional University
https://www.linkedin.com/in/nikhil-goyal
Specialization: Automation and PLC

Role: PLC and HMI Programming

- Bachelor of Technology Electronics and Communication Engineering, 9.53 CGPA as on VII Semester (08/2013 to Present)

- Senior Secondary School (12th Standard), 87% Aggregate marks, (June 2013)
- Matriculation Examination (10th Standard), 85% Aggregate Result (June 2011)
- Software Program: Rockwell Automation, Factory Talk View ME, MATLAB, Proteus, Keil
- Programming Languages: PLC Programming, Verilog, Embedded C, C, C++, SQL, Java, Data Structure
- Hardware: Rockwell PLC, HMI, SCADA, Atmel AVR Microcontroller (16/32), 8051 Microcontroller
- Training on Automation, PLC, SCADA from Prudent Solutions WLL, Bahrain,2016
- Participated in Haptic Arm Robot Competition, Lovely Professional University, 2016
- Participated in IndoUs League Competition, Lovely Professional University, 2015
- Participated in Robotryst Competition, Lovely Professional University, 2015

### 3. Mr. Veluguri Vinod, Age 20

Bachelor of Technology Mechanical Engineering, Lovely professional University https://grabcad.com/vinod.sunny-1
Specialization: CAD Design and Optimization

ROAL: Designing and Manufacturing of The PICASO 4.0

- Bachelor of Technology Mechanical Engineering, 8.1 CPGA as on V Semester (08/2014 to Present)
- State Board Certificate (12th Standard), 89.7% Aggregate Result (06/2012 to 03/2014)
- State Board Certification of Secondary Education (10th Standard), 9.3 CGPA (03/2012)
- Software Program: AutoCAD, Catia V5, SolidWorks, Ansys Workbench, Ansys APDL
- Programming Language: C, C++, HTML
- Hardware: Lath Machine, Milling, Computer Numerical Control, Shaper, 8051 Microcontroller
- Certified SOLIDWORKS Professional-Core by Dassault systems ID:C-W68QFSKGGM on 8/Jan/2016
- Training on Computational Fluid Dynamics, Technosoft Educational and Research Consultancy, Delhi, 2016
- Participated in Indo Asian Solar Challenge, Lovely Professional University
- Certified Catia, Autocad and Ansys APDL, Workbench(structural) by Canter Cadd,2016
- Certified by Trinity College of London in English, Grade -9, 2010
- Participated in Hybrid Vehicle Challenge, Lovely Professional University
- Participated in E Bike Manufacturing Competition, Lovely Professional University

## Motivation and Design Concept:

Problem Insight:

If we see present painting industry, we find most of the painting are done manually using human labor. This includes house wall painting, sign board painting, advertisement painting, graffiti, line drawings etc. Manual painting is time consuming with low throughput and high cost of labor. Sometimes, it is difficult to meet the requirement of customers because of lack of painting skills. User has to be in touch with company for regular updates. Interaction with company is tedious and industry fails to fulfill customer satisfaction.

Project Idea:

Using the concept of Industry 4.0 and Made in China 2025 satisfying Smart Machine, Smart Robotics and Smart Manufacturing for a cost effective solution for paint industry that will increase productivity, limit human intervention, avoid physical hazard and maximize the output in limited time. We propose PICASO 4.0 a Delta DIA Cloud connected Computer Numeric Control (CNC) machine based Multi-Axes Motion Control robot for Automated Vertical Painting and Vertical Laser Engraving/Cutting solution for brick walls, concrete, glass, wood etc. or any vertical plane surface that can accept paint or laser.

We have successfully developed a CNC Drawing Robot (Picture Below) based on microcontroller and stepper motor with belt driven axis and we have got drawing with precision of 0.1mm. However, the system draws/writes using pen on paper placed horizontally and has a work area of 45cmX39cm. This became the motivation for PICASO 4.0.

WORKING VIDEO LINK OF OUR CNC DRAWING ROBOT (PLEASE WATCH)

https://www.youtube.com/watch?v=77SKv8xWuLk

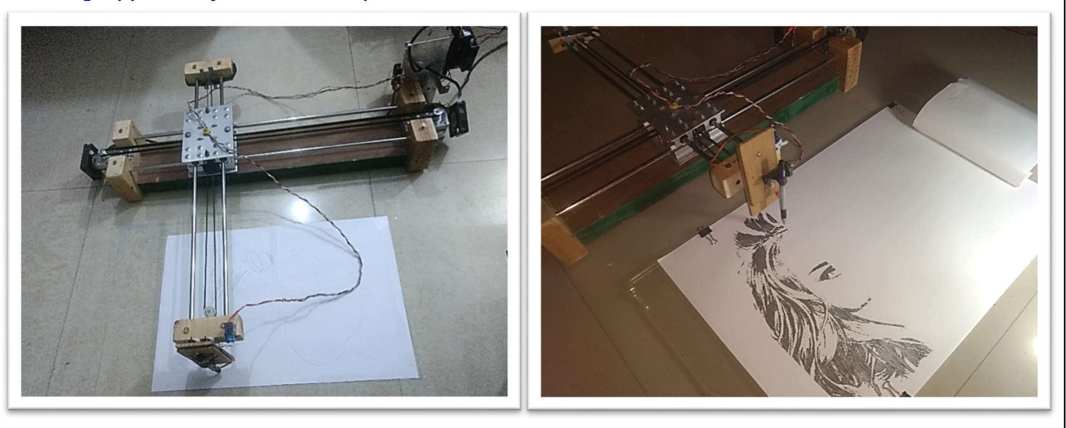
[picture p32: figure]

Fig 1: CNC drawing robot with paper | Fig 2: Drawing in raster printing mode

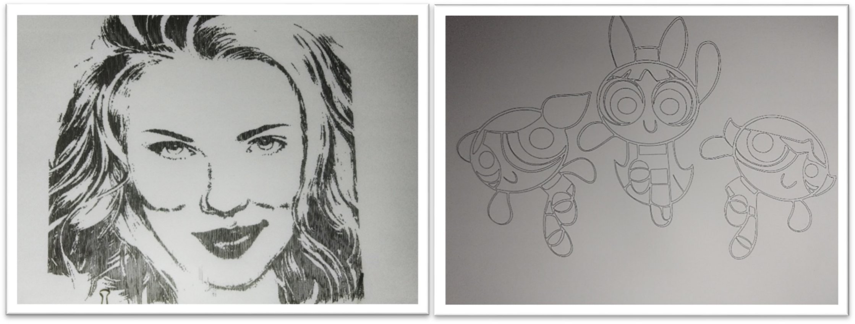
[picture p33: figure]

Fig 3: Raster printing output | Fig 4: Vector printing output

We have improved this idea to make a CNC based vertical painting/engraving/cutting robot placed parallel to a brick wall, concrete, glass wall, wood etc. which is capable of vertical painting/laser engraving customized drawing uploaded by the user on the cloud server. The system will have two tools a painting mechanism and a laser engraving We can paint walls as well as laser engrave vertical brick walls, concrete, glass, wood etc. and an extended application will be vertical laser cutting of wood or MDF.

## Objectives/Outcome:

Automate the painting process.
Increase precision in wall painting/engraving/cutting.
Vertical laser engraving/cutting and vertical painting in single machine. Increase productivity compared to manual painting.
Maximize profit in printing industry.
Reduce intake of toxic fumes from paint as only robot is involved in painting. Can work in high rise buildings where safety is a concern.
Remote monitoring of painting/engraving process through cloud.
Reduce manpower and human resource.

## Applications:

Case 1:

Customer Requirement:
A customer wants the wall of his house to be painted with his own customized design.

Solution:
Customer uploads the design to the cloud server, brings PICASO 4.0, aligns its painting tool towards wall, put it into painting mode, set painting area and enjoy the output.

Case 2:

Customer Requirement:
A customer has a glass door at his office entrance and he wants his company’s logo to be engraved on it but he does not want to invest in a new door and also he wants to avoid disassembly and reassembly of door.

Solution:
Bring PICASO 4.0, align its laser tool towards glass door, upload company’s logo to cloud server, put it into laser engraving mode, set engraving area and enjoy the output.

Case 3:

Customer Requirement
A customer has a large factory that has a concrete wall around its perimeter. Customer wants his perimeter to be painted with least labor cost and minimum time.

Solution:
Configure PICASO 4.0 to move around the perimeter wall and paint.

## Robot Design:

Our system is divided into three axes (X, Y, Z). The design consists of a base chassis on which the whole system stands. The base chassis houses all the servo drives, power supply, PLC, wiring, servo motors, etc. The base chassis has four servo motors that are attached with gear box, which are further attached with wheels. The chassis along with the wheels and servo forms the X axis. The X axis moves horizontally parallel to wall or work surface. Above the chassis runs vertically four aluminum extrusion which supports the Y axis for the system. The Y axis moves vertically up or down using two lead screw with two split nuts attached to the base of a sliding rack. The lead screws are rotated by servo motors coupled to it and are placed inside the chassis. The Z axis is above the rack of Y axis and moves two tools toward or away from the wall. We can place the robot in two orientations: one with printing head towards wall for printing and other one is laser towards wall for engraving. An HMI is attached to the side of the robot for real time monitoring, start, stop, emergency stop, etc.

PICASO 4.0 PRODUCT DESIGN ANIMATION :: https://youtu.be/C1ulfhZpyTI

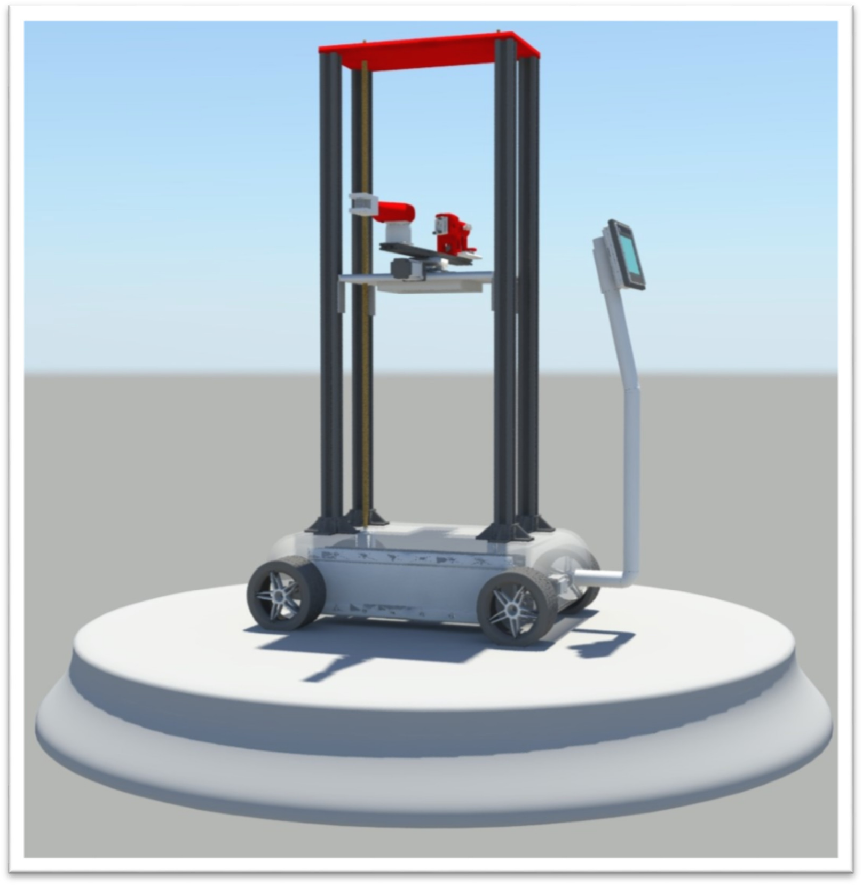
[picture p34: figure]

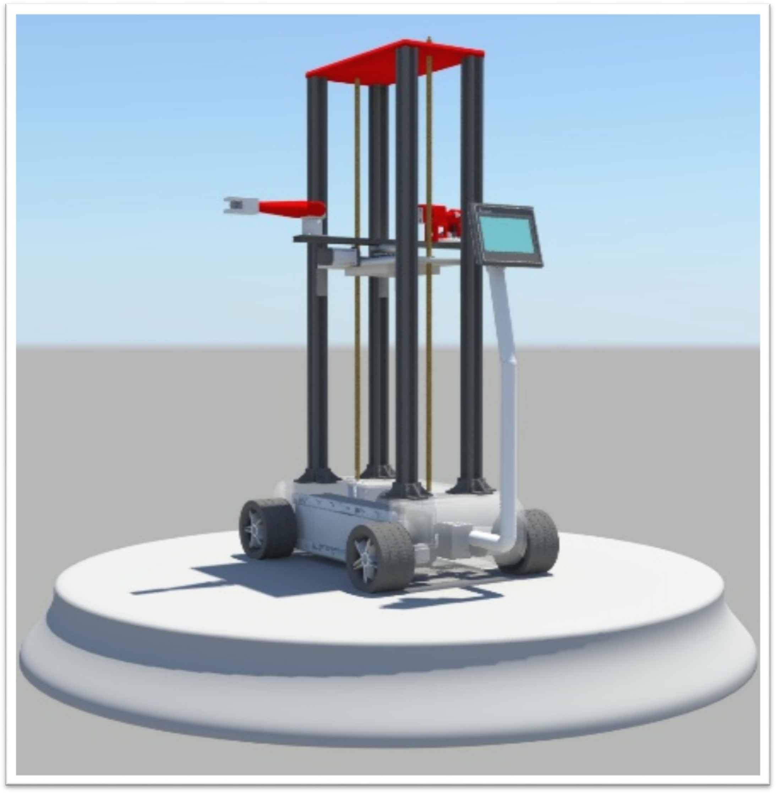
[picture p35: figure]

Fig: Isometric View with all assembly

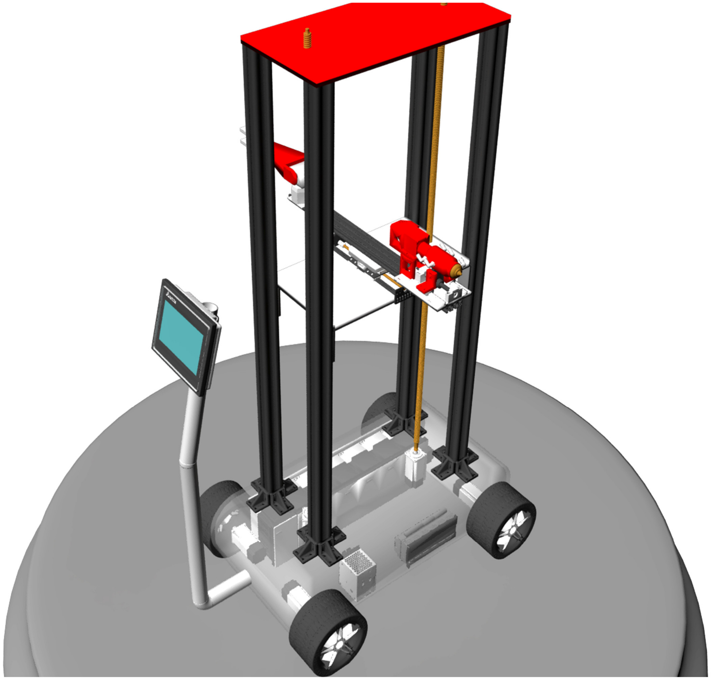
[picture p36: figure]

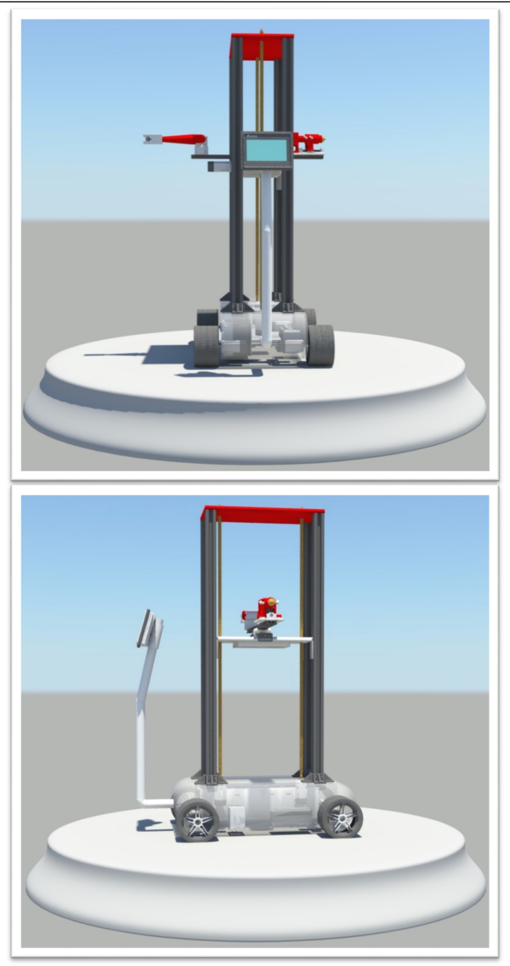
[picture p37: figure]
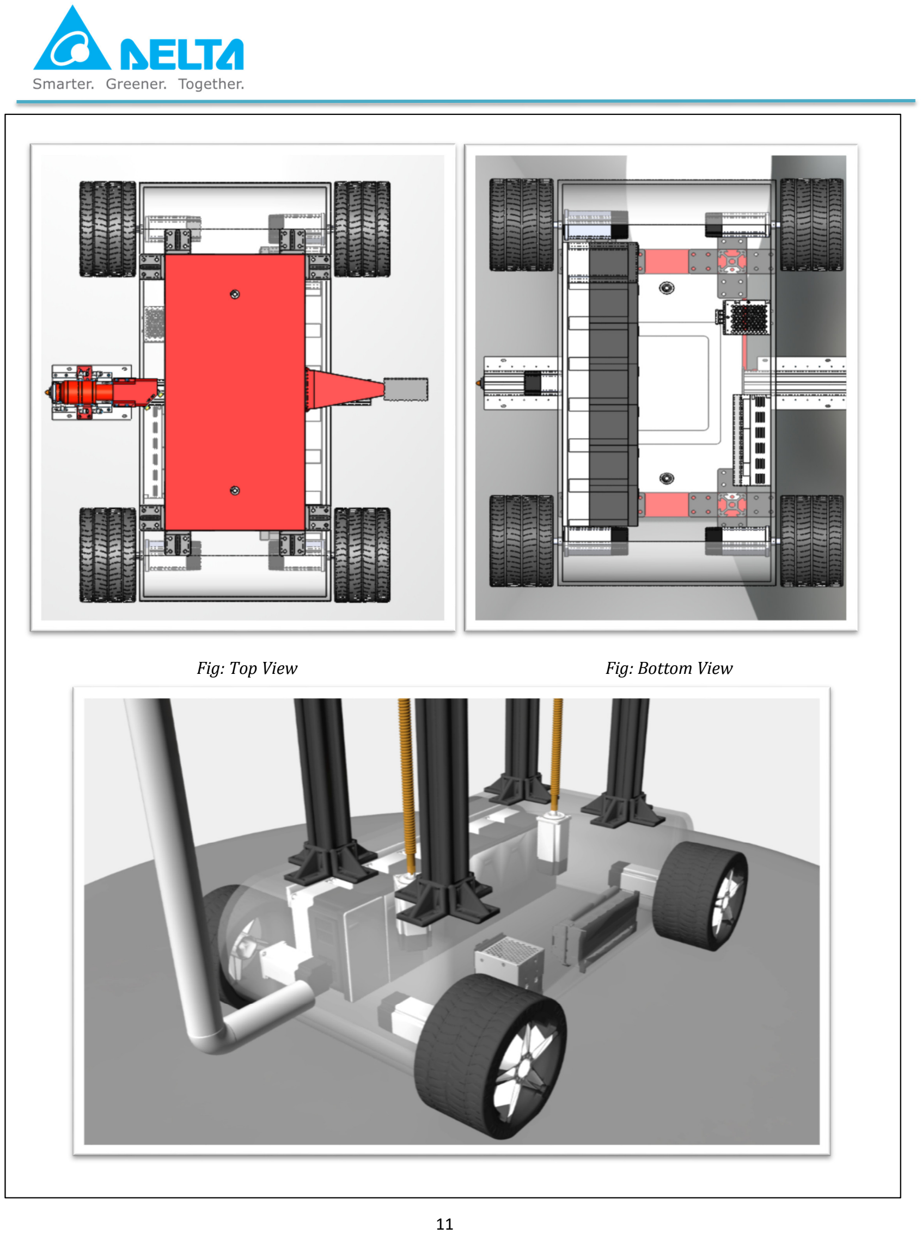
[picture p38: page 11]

Fig: Top View | Fig: Bottom View

## Mechanical Drawings:

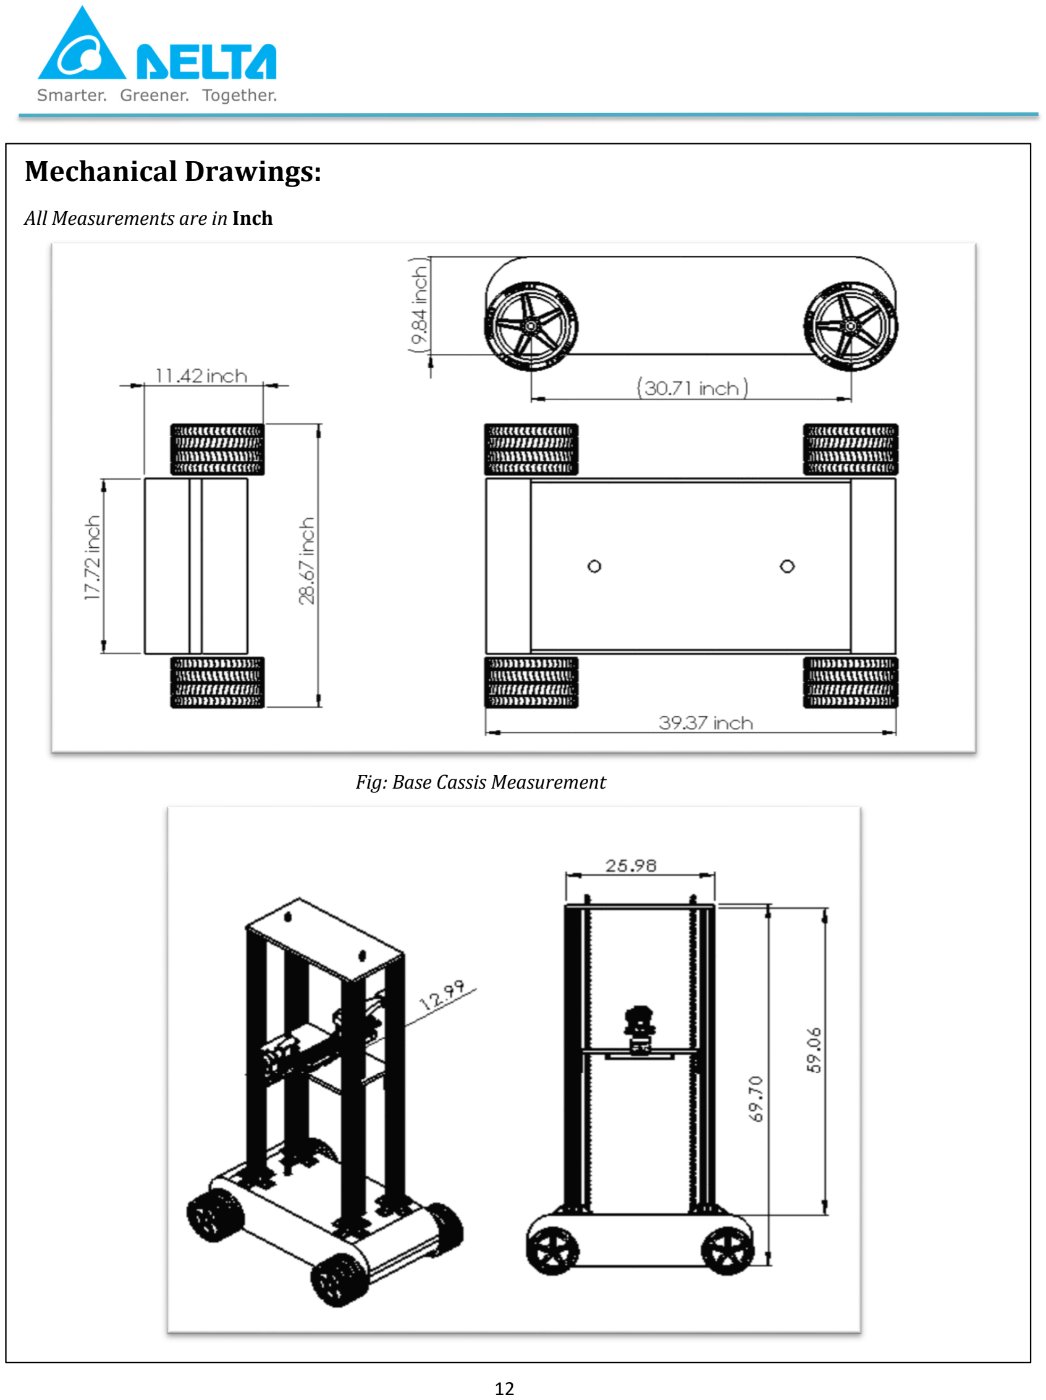
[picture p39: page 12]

All Measurements are in Inch

Fig: Base Cassis Measurement

## Design Analysis:

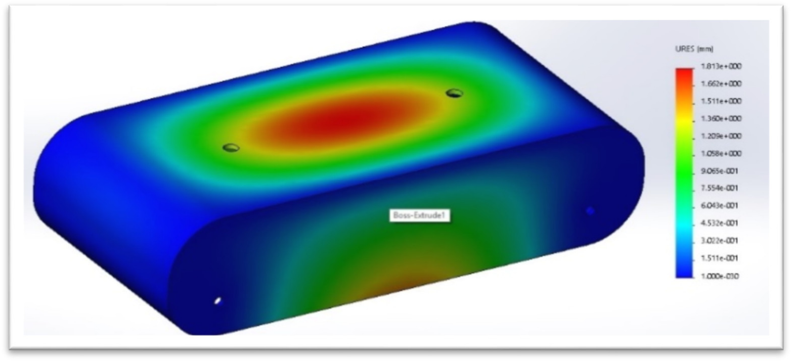
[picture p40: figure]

Fig: Displacement Analysis

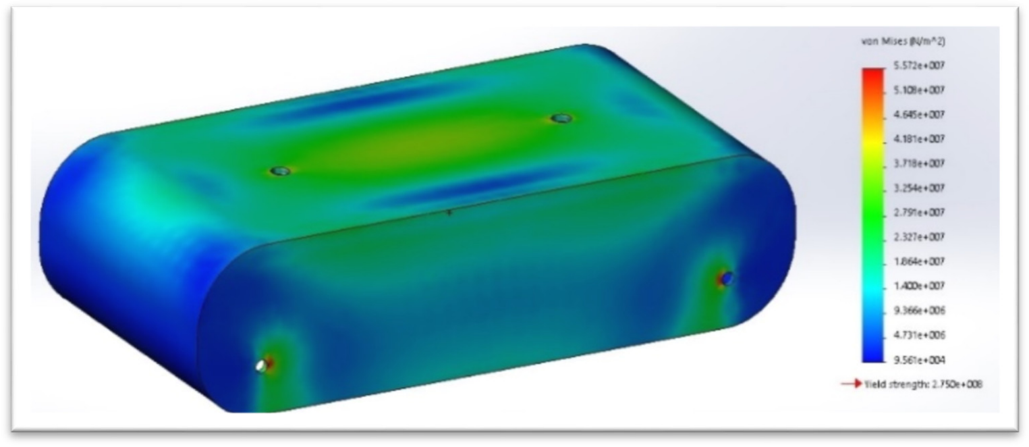
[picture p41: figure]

Fig: Stress Analysis

Force | 2000N
Displacement | 1.8mm

## Motion Control:

In this project we are using multiple servo motors for controlling X, Y, Z axis motion.

1. In the X Axis we will use four servo motors that gear box coupled with four wheels in the base of the robot that will work in coordination to move the whole robot parallel to the wall. Feedback from ultrasonic sensors placed on ends of Y axis rack, facing the wall, continuously measure distance to maintain Y axis parallel to wall.
2. In the Y Axis we will use two servo motors directly coupled to two lead screw and will also work in lock step / synchronization.
3. In the Z Axis we will use one servo motor to move the printing head / laser head near and away from the wall.

G-Codes will be used for motion control with both linear interpolation and circular interpolation.

## Tool Control:

In this robot we will be controlling two tools that are facing opposite to each other in the design and mounted on the Z axis. One tool will be a painting head another will be a laser head. According to our need, we will place the robot in such way that the required tool will face the wall. After which the axis for that job will be assigned and the robot will move accordingly. (For the laser engraving mode the axis (-X, +X) will work vice-versa.

M-Codes will be used to control the paint head and the laser head. Only one will be activated at one time. We will be controlling the laser intensity as well as paint outflow from the Z axis.

Continuous calculation of distance between wall and the Y axis will be done using high accuracy industrial ultrasonic sensor that will give feedback for the system so that it always remains parallel to the wall. Four motors of the x axis will be differentially speed controlled to maintain equidistance between the tool and the wall or surface. Any compensation will be done using the z axis.

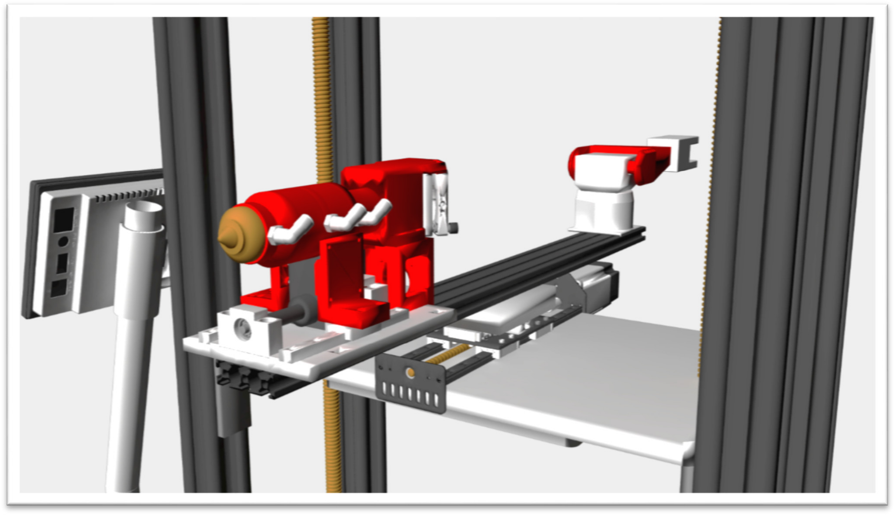
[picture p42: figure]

Fig: Tool Mounted on Z-axis and Facing Opposite

## Robot’s Work Space:

- Cartesian Coordinate Robot
- The robot can work only on flat-floor and flat-wall.
- Can’t move on too much slanted floor (15 Degree Safe Limit)
- Cannot move pass locked door or closed door.
- Need clearance in his path for proper movement and operation.

## Uncertain Error Handling:

- PICASO 4.0 will pause all its work.
- Emergency alarm will be switched on and emergency light will be displayed.
- Massage notification will be visible on HMI and will also be uploaded on cloud.
- Robot will need operator’s command to resume work after solving problem.

## Block Diagram


## Robot Operation:

Step 1 > User will upload the image required for vertical painting or engraving with size specification to cloud server and will select the required mode i.e. painting or engraving.
Step 2 > The Image is rasterized and processed to generate G-Codes and M-Codes for the robot in the server.
Step 3 > The PLC will download the G-Code file.
Step 5 > PICASO 4.0 is placed along the wall with specific tool facing the wall.
Step 4> PICASO 4.0 will start engraving or painting according to the G-codes and M-codes.
Step 5> Live work status is uploaded to the cloud for supervisory purpose.

## Innovative Planning and Value

- PICASO 4.0 can be used for both horizontal and vertical applications with slight modification in design.
- PICASO 4.0 don’t have work area limitation.
- PICASO 4.0 is designed using standard industrial parts and accessories (e.g.: v-slots, lead screw, etc.).
- Easy to assemble and disassemble the PICASO 4.0
- PICASO 4.0 is connected with cloud thus accessible from anywhere.

## Cost Analysis, Reasonability and Feasibility

As we are using all parts according to the industrial standards, we are have very cost effective structure. In this we need to manufacture only the base chassis in which we have to use milling and welding process. Thus Manufacturing time is low and will be done in a reasonable cost.

## Components Specification & Bill Of Materials

Serial Number | Product Name | Delta Product Code | Quantity | Description
| DELTA PRODUCTS
1 | Wireless Module | DVW-W02W2-E2 | 1 | To connect with internet
2 | Power Supply (24V Output) | PMC Panel Mount Power Supply (24V Output) | 1 | To provide 24V to the PLC
3 | PLC | AS 300 / AH 500 Series | 1 | Main controller which accept the input through HMI and cloud server and do control according to ladder logic.
4 | HMI | W105B (10 Inches) | 1 | To observe the status of the robot on the field and to control it, we are using 10 inches’ screen.
5 | Pressure Sensor | DPA 01 M/P Series | >1 | To check the pressure of the paint fluid at Inkjet Sprinkler so that spray can perform at constant pressure or flow.
6 | Motor Driver | Delta Servo Drives | 7-8 | To drive all Axes motors
7 | Servo Motor | Delta Servo Motor | 7-8 | To move all Axes
8 | Planetary Gear Box | Delta Product | 4 | To attach between wheels and servo motor of X axis
9 | Linear Motion Product | Delta Ball Screw Driven Delta Product (Z- AXIS) | 1 | For Z-Axis
| OTHER PRODUCTS
10 | Multiple High Precision Ultrasonic Sensor | Third Party | 4 | For calculating distance from wall
11 | Limit Switch | Third Party | 4 | For limiting Y Axis and Z Axis motion
12 | Inkjet Sprinkler | Third Party | 1 | For sprinkling paint on wall
13 | Power Supply (5V, 5Amp) | Third Party | 1 | For powering microcontrollers and other peripherals
14 | Microcontroller | LPC 2148 ARM TDMI (Third Party) | 1 | For sensor data acquisition

15 | High Power Carbon Dioxide LASER | 80 Watt (Third Party) | 1 | For engraving on wall
16 | Wheels | Third Party | 4 | For moving the robot along X Axis
17 | Flexible Motor Coupler | Third Party | 2 | For coupling with lead screw
18 | Laser Head and Optics | Third Party | 1 | For focusing laser beam
19 | Linear Bearing | Third Party | 8 | For smooth movement of Y Axis rack on aluminum extrusion
20 | BLDC Blower Fan | Third Party | 4 | For cooling Drives
21 | Fastener | Third Party | Multiple | For assembly of Robot
22 | Wire | Third Party | Multiple | Wiring
23 | Aluminum 6063 T6 Extrusion 6 Feet | Third Party | 4 | For construction of Y axis
24 | Wire Connector | Third Party | Multiple | Wiring
25 | Aluminum L Joints | Third Party | 24 | For construction of Y axis
26 | Lead Screw 16mm Diameter 4mm Pitch | Third Party | 2 | For Y axis
27 | Bearings | Third Party | Multiple | For putting with rotary parts

Future Scope:

1. We can modify the system to perform a complete wall painting process including buffing, cleaning, moisture sensing, painting, drying, and final image processing based monitoring.
2. Addition of gyroscope and accelerometer data fusion algorithm with PID can be used to painting on uneven surface. The robot will automatically compensate the slating of surface.
3. We can do large scale 3D printing by attaching specific tool.
4. Horizontal printing on roads, floors, any horizontal surface (e.g. Zebra Crossing Printing).
5. Connected machines (IOT) that will do multiple section of a wall at same time, working hand in hand to complete a task in much less time.

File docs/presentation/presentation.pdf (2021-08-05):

# PSP : Pick, Sort and Place Bot


### delta2021090 : Team DNS 1. Ninad Jangle 2. Karthik Swaminathan 3. Dhairya Shah

### Veermata Jijabai

Technological Institute,

### Mumbai, India

2021.07.24

# THE PROBLEM


Delta Confidential | 2
- When dealing with items of varied sizes, the packaging industry is handicapped by relying on manual labour or a large succession of machines to handle those different items.
- Similar is the case with items to be packed and shipped for a certain locality or location.
- The first being too inefficient and the latter being too capital intensive, for midsize companies, both are a resource problem.

# STATISTICS


The global Packaging Robots Market was valued US$ 2.53 Bn in 2019 and is expected to reach US$ 6.40 Bn by 2027, at a CAGR of 14.18 % during a forecast period.

The price of Labor has increased exponentially while the price of robots has dropped significantly. For the field of custom packaging, which is still heavily dependent on the human resource, this is a money pit.

# OUR TIMELINE


# BASE VISUALIZATION


BOT Assembly | Electrical Panel

# OUR SOLUTION


1. Our solution is to provide a scalable, economical pick and place bot.
2. It is a XYZ Gantry based design which maps and places an object in 3 dimension plane
3. Variable sized input items will be coming on a conveyor

# OUR SOLUTION


4. These items will be scanned and the orientation, co-ordinates, shape and dimensions of the input boxes will be emulated by image processing taken by Delta’s Machine Vision System.
5. Then the bot will be pick and place them into bigger output containers.
6. The pick and place operation will be carried out using suction generated from a vacuum blower.

# BLOCK DIAGRAM


Suction

# ALGORITHMIC WORKFLOW


# STRUCTURAL EXPERIMENTATION


VON MISES STRESS ANALYSIS

- We experimented with the concept, design and materials to find the best compromise
between quality and cost.
- Thereby, we were able to construct the designs in very industry friendly rates and quality.
- We talked to many vendors and performed multiple analyses during selection of the materials and designs.

# STRUCTURAL ANALYSIS


URES DISPLACEMENT ANALYSIS | STRAIN ANALYSIS

# INTEGRATION PYRAMID

Mechanical Structure; Manipulated using the automation equipment to create productive motion and realise the goals of PSP Bot.; Gantry Frame, C channels, ...; Automation and Motion Components; Devices Communicate each other to realise the logic based on algorithm. ● Motion Controller PLC: Controls the Motion ● HMI: Human-Machine Interfacing ● Machine Vision System: Image and object detection ● Servos and Servo Drives: For motion in XYZ axes and for rotation ● Lidar Sensor: For measuring depth ● Other Sensors and devices; Algorithm; The software logic that controls the actions of the PSP BOT

# MECHANICAL STRUCTURE AND DESIGN


# SORTING ALGORITHM


- We have tried to implement a 3D Packaging algorithm
- It works on the principle of efficient fit of items in the number of available output container or bins
- This basically localises the items and maps it in 3-Dimension.

# INNOVATION AND FEATURES


1. Economical and Timely Solution: Production cost and time consumed are relatively low as compared to ideal industry
2. Mobility : Can be easily disassembled and moved.
3. Scalable : By making minor design changes, size of the bot can be adjusted as per required application
4. Vacuum Cleaner/ Blower based Suction : Ensures friendly and efficient Pick and Place operation, End effector is easily changeable as per surface nature of the input items.
5. Device Interfacing : Easier Interfacing implemented using Delta’s IIOT smart solution.


6. Customizable End Effector : For different input sized boxes
7. Efficient Algorithm : A 3D Packaging Algorithm which minimises the space wastage
8. Conveyor: Input Items will be coming on a conveyor, the gantry system will pick and place them into output boxes.

# APPLICATIONS AND USES


1. Multinational Supply chain Companies (like Amazon, Flipkart, Alibaba, etc) : Packaging and shipping parcels and items based on common location in a single container. This includes Items of:
- Variable Sized Packaging
- Location based Packaging
2. Customised Subscription Boxes : Packaging custom products into a common container based on
subscriptions made.

# FUTURE SCOPE


1. Transforming Bot into a ready, full fledged economical Industrial product.
2. Making our algorithm more robust and dynamic for different inputs and service parameters.
3. Integrating absolute bot control and other device communications using advanced IIoT to fully automate the process and establish an easier control flow.
4. Also, integrating the current model with Machine Learning could definitely make it more smart and efficient.



Smarter. Greener. Together.

To learn more about Delta, please visit www.deltaww.com

# Thank You

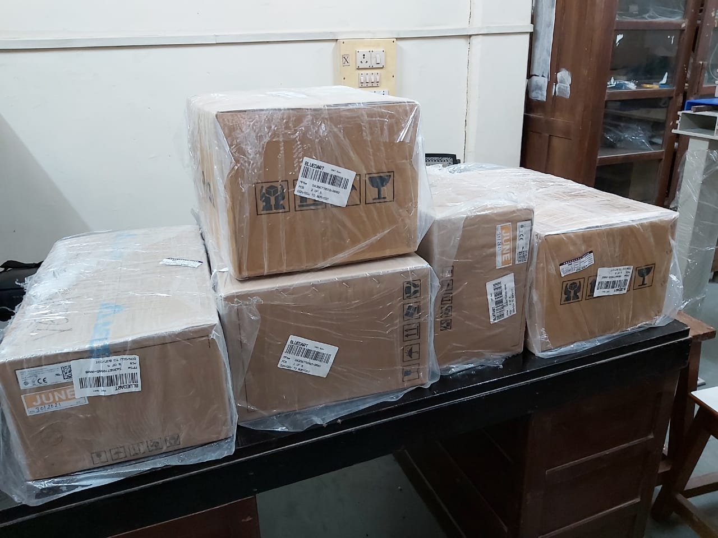
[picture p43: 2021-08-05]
assets/products.jpeg

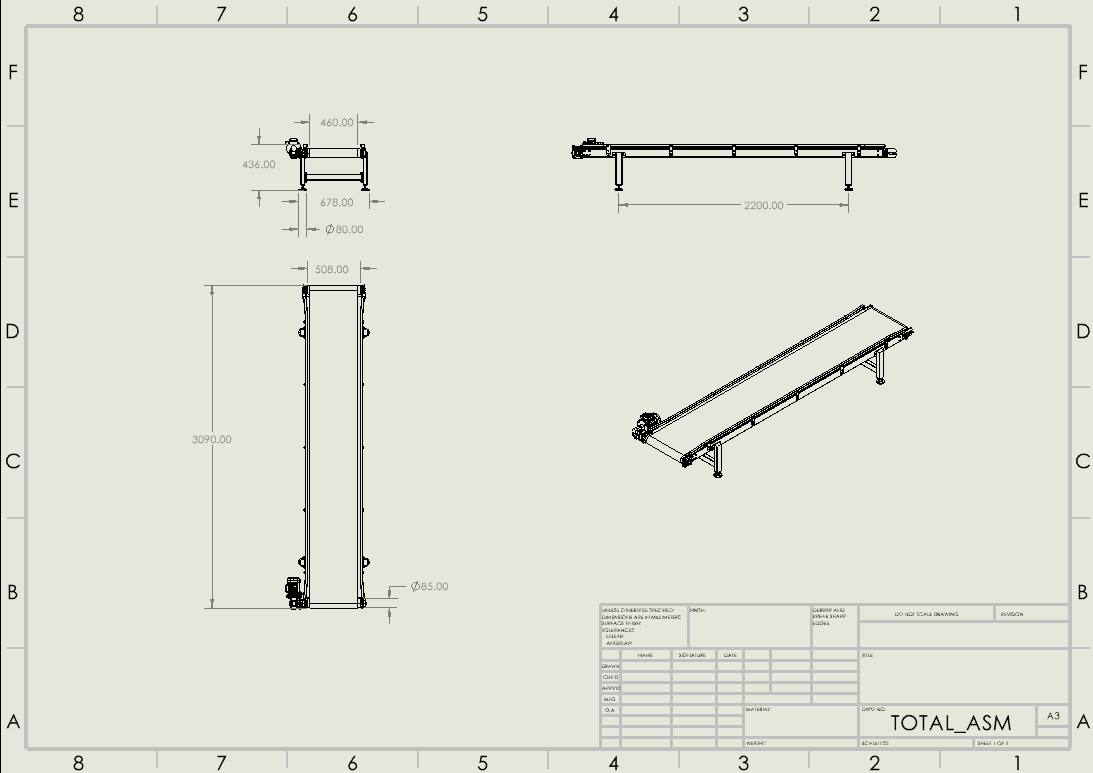
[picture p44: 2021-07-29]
docs/general_data/Drawings/Conveyor_Drawing.png

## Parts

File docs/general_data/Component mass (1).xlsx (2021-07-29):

 |  |  |  | Aluminium - 6061
Part | Mass(kg) | Quantity | Density(kg/m^3) | Material | Total Weight(kg) | Solid/Hollow
Slider_x | 7.6 | 2 | 2700 | Aluminium | 15.2 | Hollow
Ibeam_x | 10.58 | 2 | 2700 | Aluminium | 21.16 | Hollow
Slider_cover_x | 6.61 | 2 | 2700 | Aluminium | 13.22 | Solid
Guide_rail_y | 17.82 | 1 | 2700 | Aluminium | 17.82 | Hollow
Guide_rail_z | 29.01 | 1 | 2700 | Aluminium | 29.01 | Solid
Guide_motor_part_z | 3.13 | 1 | 2700 | Aluminium | 3.13 | Hollow
L_shaped_z | 3.73 | 1 | 2700 | Aluminium | 3.73 | Solid
Rod_z | 2.65 | 1 | 2700 | Aluminium | 2.65 | Solid
Main_vertical_support_rods + supports+ rectangular plate | 62.49 | 4 | 7890 | Steel | 249.96 | Hollow
Ball Screw(Z) | 2 | 1 | 7890 | Steel | 2 | Solid
Wheels_Z | 1 | 4 | 2700 | Aluminium | 4 | Solid
 |  |  | 2700 | Aluminium
 |  |  |  | TOTAL | 361.88
Approx weight (on x) |  |  |  |  | 110 - 150
Approx weight (on y) |  |  |  |  | 70 - 80
Approx weight (on z) |  |  |  |  | 30 - 40

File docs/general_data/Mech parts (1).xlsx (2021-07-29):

Standard | Links | Material | Cost
Steel tubes | http://www.bhushantube.com/square-rectangular-hollow-sections-specification.html | Steel
Rack and pinion | https://pearlengineers.com/rack-and-pinion.html | Mild Steel
Nuts | https://www.industrybuying.com/
rollers | https://in.misumi-ec.com/vona2/mech/M1100000000/M1105000000/M1105040000/ https://www.ubuy.co.in/catalog/product/view/id/19813883/s/2-pcs-2-inch-v-shaped-groove-wheel-for-sliding-door-steel-track-rail-sliding-gate-roller-with-bracket | steel | 1130
ball screw | https://in.misumi-ec.com/vona2/maker/misumi/mech/M0100000000/M0114000000/
Vertical arm rod
L shape(Angle) | https://www.sandeepsteels.com/M_S_Angle.htm
Wire Oganisers
Gears | gears' (https://in.rsdelivers.com/product/rs-pro/grss07-15b/rs-pro-steel-15-teeth-spur-gear-07-module-3mm/1827863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) | steel | 950
Rail | https://www.pbh.in/shop/bgr-15-rail-length-520mm-61517?search=bgr | steel | 1193
Rest | https://robokits.co.in/mechanical-parts https://www.indiamart.com/proddetail/hex-bolt-f-thread-m16x50-13636166897.html
Gripper | ZPR25CNK10-08-A10 SMC | SMC 25mm Flat with Rib NBR Suction Cup ZPR25CNK10-08-A10 | 725-333 | RS Components (rsdelivers.com) (https://in.rsdelivers.com/product/smc/zpr25cnk10-08-a10/smc-25mm-flat-with-rib-nbr-suction-cup-zpr25cnk10/0725333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)
dragchain | https://robu.in/product/10-x-10mm-1m-cable-drag-chain-wire-carrier/ https://www.sibasselectric.co.in/drag-chains.html |  | 1000/m
Custom
slider plates
Aluminium |  |  | 150/kg
I beam | Mild Steel I Beam Wholesale Trader from Pune (vijaysteel.in) https://www.jspl.net.in/mild-steel-beam.html (https://www.vijaysteel.in/mild-steel-i-beam.html) | Mild Steel | 33-45/kg | 2700
Y beam
Z Vertical
Z Top Plate
Z L shape
L shape + rib (supports) | Blue Color 0.6 Mm Ms Sheet Iron 3 Hole Angle Bracket, Size: 17 Inch, Rs 85 /piece | ID: 22216625848 (indiamart.com) (https://www.indiamart.com/proddetail/3-hole-angle-bracket-22216625848.html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) | Mild Steel
Fabrication
vertical columns
Custom Part Designers: | https://www.precimetal.co.in/ https://www.precicam.in/ https://www.gemsons.com/ https://raltech.in/
Air Compressor | https://toolz4industry.com/product/eurostar-3-hp-50-litres-air-compressor/
Electrical
MCBs | MCBs - Buy Single, Double, Three, Four Pole MCB Online in India (bestofelectricals.com) https://shop.schneider-electric.co.in/easy9-mcb-1p-10a-b-10000a-240v.html (https://www.bestofelectricals.com/protection-devices/mcbs)
relay | 24VDC SCHNEIDER ELECTRIC Power Relays | element14 India https://in.element14.com/finder/38-51-0-024-0060/relay-spdt-250vac-6a/dp/1169353 (https://in.element14.com/c/switches-relays/relays/power-relays?brand=schneider-electric&coil-voltage=24vdc)

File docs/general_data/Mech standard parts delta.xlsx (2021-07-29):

STANDARD MECHANICAL DELTA PSP BOT PARTS: TO BE BOUGHT
Major Part | Part Name | Specifications/ references | Quantity | Contact No | Site Links/ | material
X - axis | Rack and Pinion X | Length of rack: 1500mm Pinion Module - 2 Rack Module - 2 No. of teeths(Pinion) -18 | 2
 | Gear coupling |  | 2
 | UHMW pads | Length - 400mm Width - 12mm Height - 20 mm | 4
 | Drag Chain | Length - 1800mm https://robu.in/product/10-x-10mm-1m-cable-drag-chain-wire-carrier https://www.sibasselectric.co.in/drag-chains.html | 2
Y- axis | Rack and Pinion Y | length of rack - 1200mm Pinion Module - 2 Rack Module - 2 No. of teeths(Pinion) -18 | 1
 | Drag Chain | Length - 1500mm | 1
 | Gear coupling |  | 1
 | UHMW pads | Length - 270mm Width - 13mm Height - 30 mm | 2
 | V shaped guide rails | Length - 1200mm | 2
 | Rollers | https://in.misumi-ec.com/vona2/detail/110302649620/?CategorySpec=00000196577%3a%3af | 4
Z - axis | Linear Guide ways | Length - 600mm https://in.misumi-ec.com/vona2/detail/110302271870/ | 2
 | Ball screw | Length - 600mm (thread/winded length) Diameter -10mm Lead - 10mm https://hiwin.us/wp-content/uploads/ballscrews.pdf | 1
 | Ball screw support units | https://in.misumi-ec.com/vona2/detail/110300080010/ | ~
 | Coupling |  | 1
 | Bearings
 | Vacuum - Suction gripper |  | 1
 | Drag Chain Linear |  | 1
 | Drag chain Rotation *
 |  | * - Conditions apply

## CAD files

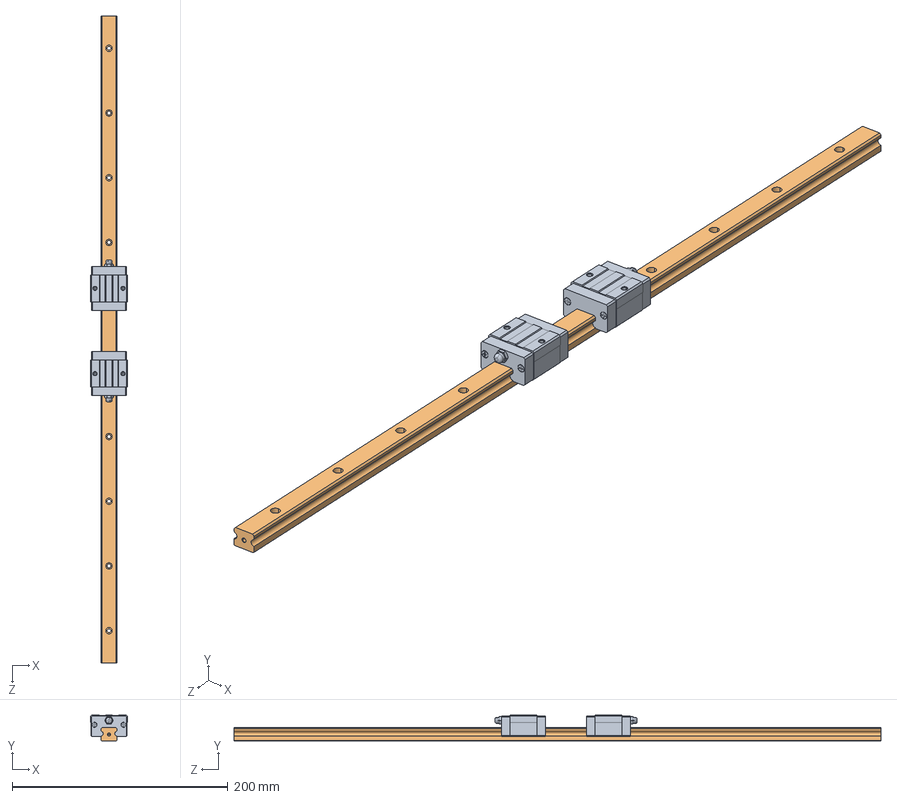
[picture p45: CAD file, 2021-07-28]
cad_files/Guide_Rails/RV2RL24L_600_TMC.sldasm
34.0 x 24.0 x 600.0 mm
RV2RL24L_600_TMC_3 x 2
RV2RL24L_600_TMC_6

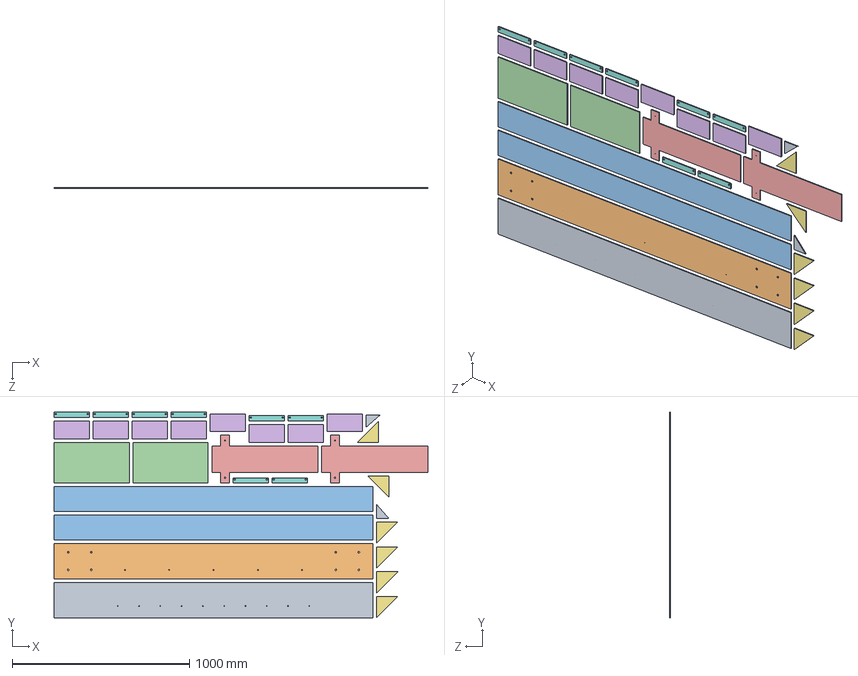
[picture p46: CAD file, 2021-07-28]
cad_files/PSP_BOT_CAD/Nesting/Nesting(5mm).SLDASM
2110.0 x 1160.0 x 5.00 mm
Y_Plate_3
Y_Plate_1
Y_Plate_2 x 2
Z_Plate_2 x 2
Z_Plate_1 x 2
C Covering 1 x 8
Motor Extension Rib x 6
C Covering 2 x 8
Rib x 2

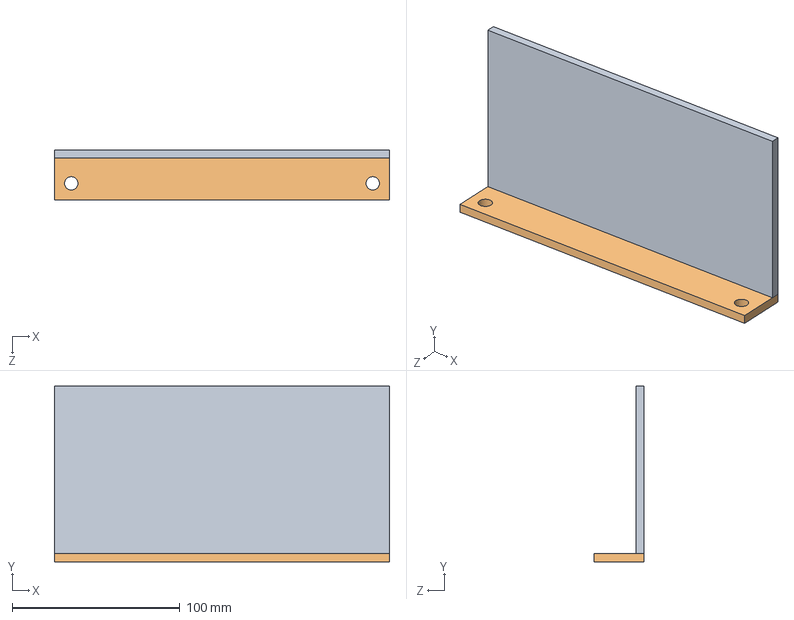
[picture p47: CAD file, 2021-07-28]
cad_files/PSP_BOT_CAD/X_Assembly/C Covering/C_Covering.SLDASM
200.0 x 105.0 x 30.0 mm
C Covering 1
C Covering 2

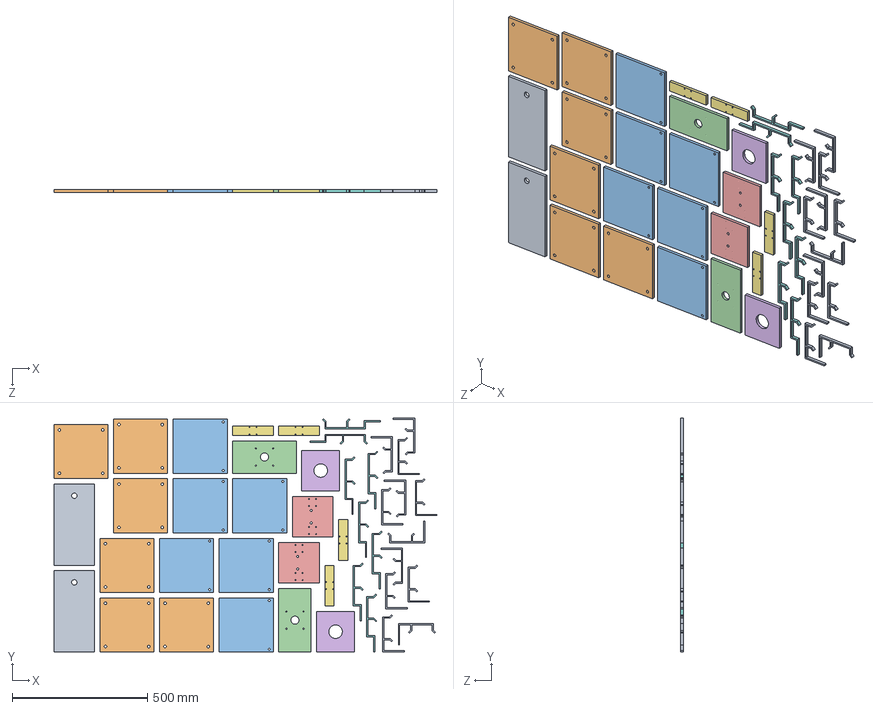
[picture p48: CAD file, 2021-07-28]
cad_files/PSP_BOT_CAD/Nesting/New_Nesting(10mm).SLDASM
1414.6 x 864.0 x 10.0 mm
Z_Top_Plate x 2
Base_Plate_X x 6
Top_Plate_X x 6
Motor Extension Plate x 2
Horizontal_Plate x 2
Vertical_Plate x 2
Lower_Section x 4
Drag_Chain_Bracket_Y x 8
Drag_Chain_Bracket x 12

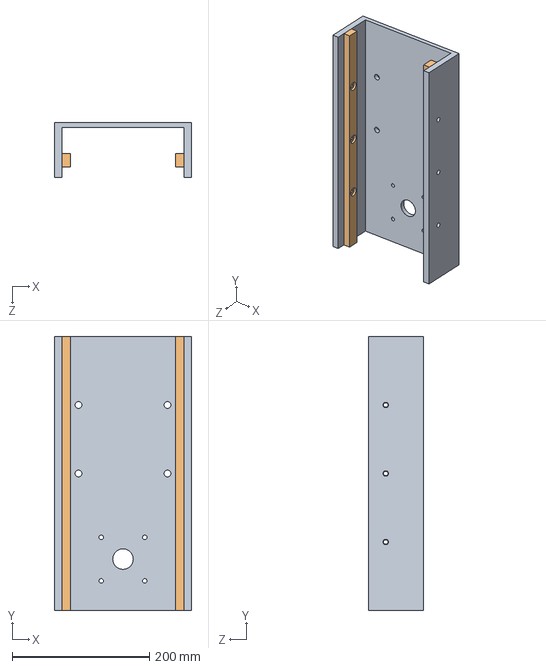
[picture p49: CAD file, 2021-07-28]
cad_files/PSP_BOT_CAD/Y_Assembly/Slider_Plate/Slider_New.SLDASM
200.0 x 400.0 x 80.0 mm
Slider_With_Roller
UHMW_pad x 2

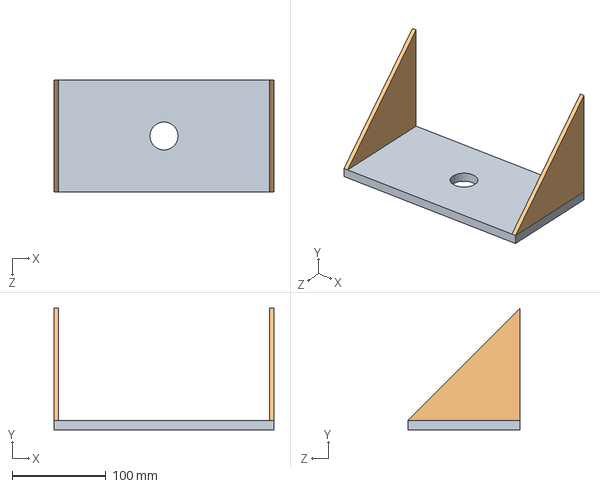
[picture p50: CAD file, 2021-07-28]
cad_files/PSP_BOT_CAD/Z_Assembly/Motor_Extension/Motor_Extension_Z.SLDPRT.SLDASM
235.0 x 130.0 x 120.0 mm
Motor Extension Plate
Motor Extension Rib x 2

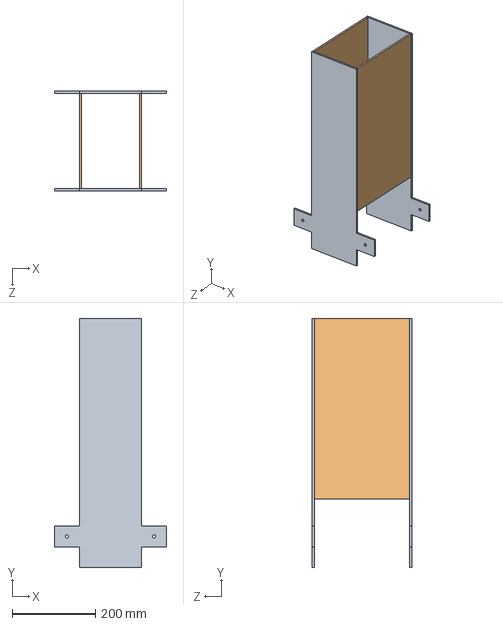
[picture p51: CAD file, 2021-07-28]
cad_files/PSP_BOT_CAD/Z_Assembly/Z_Column_Assembly/Z_Column_Assem.SLDASM
270.0 x 600.0 x 240.0 mm
Z_Plate_1 x 2
Z_Plate_2 x 2

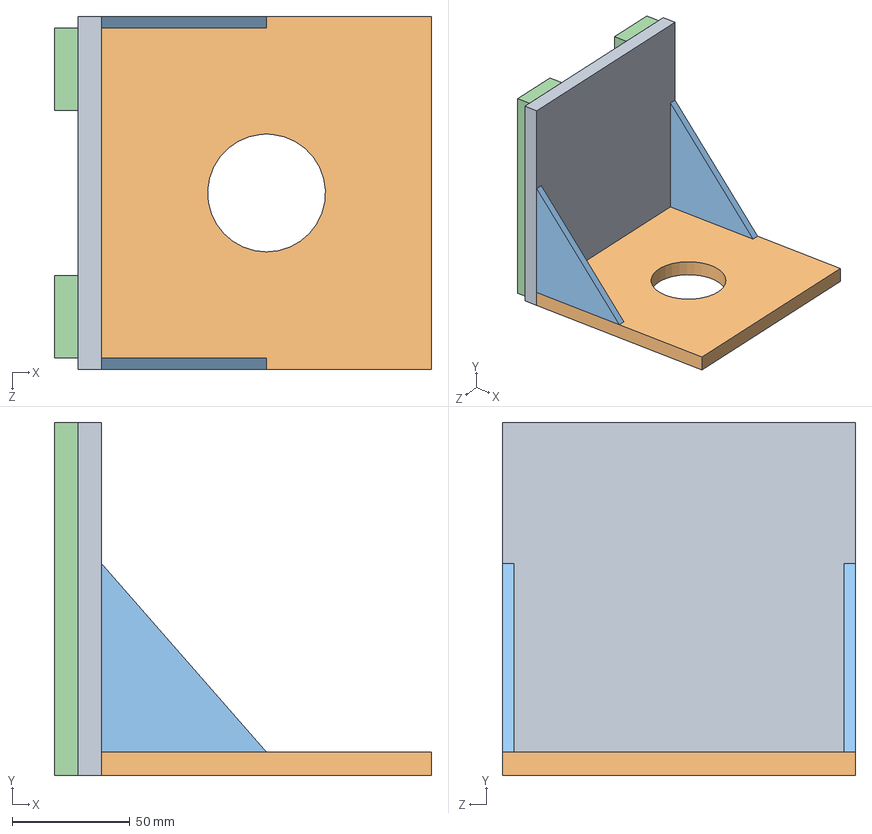
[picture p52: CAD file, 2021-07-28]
cad_files/PSP_BOT_CAD/L_Assembly/Z_L_Shape.SLDASM
160.0 x 150.0 x 150.0 mm
Horizontal_Plate
Vertical_Plate
Rib x 2
Lower_Section x 2

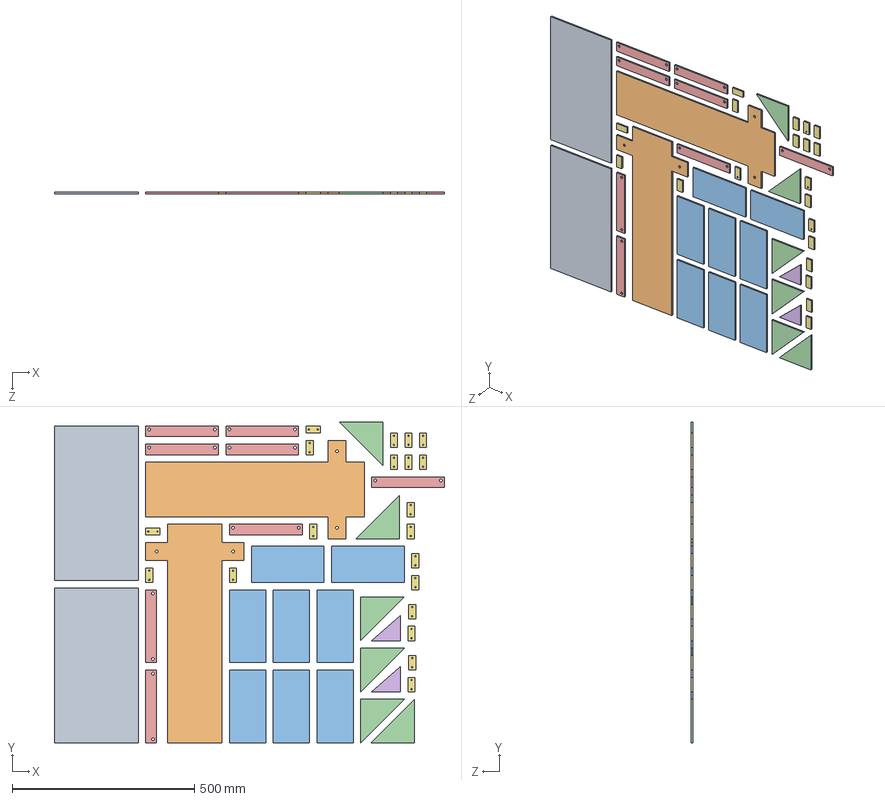
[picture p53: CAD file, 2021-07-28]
cad_files/PSP_BOT_CAD/Nesting/New_Nesting(5mm).SLDASM
1070.0 x 880.0 x 5.00 mm
Z_Plate_2 x 2
Z_Plate_1 x 2
C Covering 1 x 8
Motor Extension Rib x 6
C Covering 2 x 8
Rib x 2
Bracket_Plate x 20

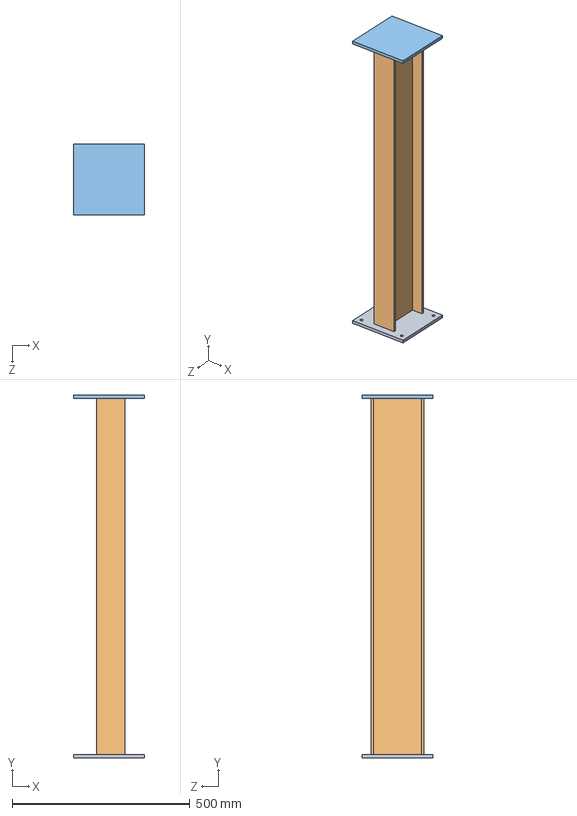
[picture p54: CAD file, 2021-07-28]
cad_files/PSP_BOT_CAD/Vertical_Column/X_Vertical_Column.SLDASM
200.0 x 1020.0 x 200.0 mm
Base_Plate_X
ISMB 150
Top_Plate_X

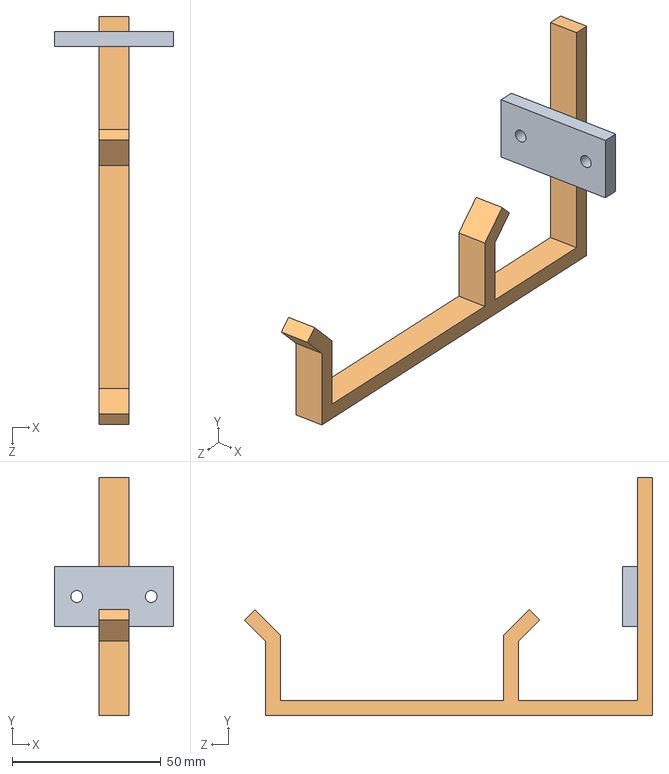
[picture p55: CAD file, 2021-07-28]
cad_files/PSP_BOT_CAD/X_Assembly/Drag_Chain_Bracket/Drag_Chain_Assem.SLDASM
40.0 x 80.0 x 137.1 mm
Bracket_Plate
Drag_Chain_Bracket

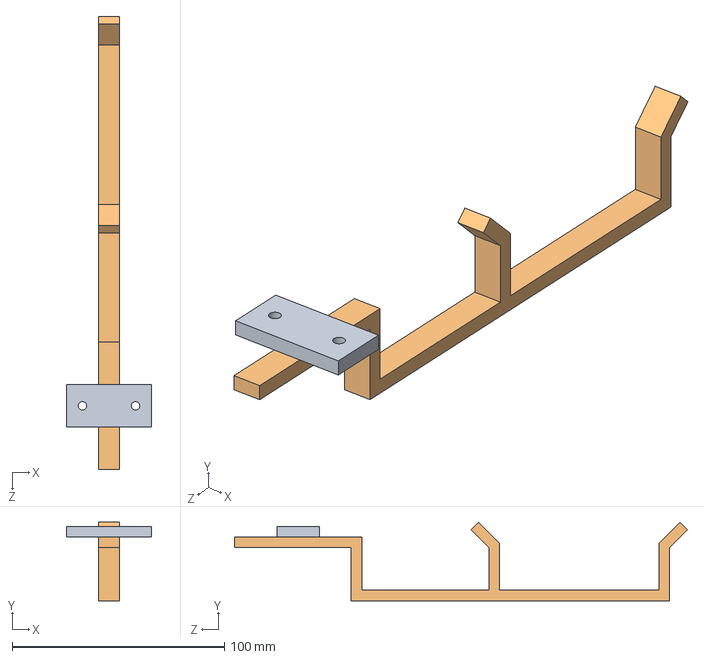
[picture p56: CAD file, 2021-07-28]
cad_files/PSP_BOT_CAD/Y_Assembly/Drag_Chain_Bracket_Y/Drag_Chain_Assem_Y.SLDASM
40.0 x 37.0 x 213.5 mm
Bracket_Plate
Drag_Chain_Bracket_Y

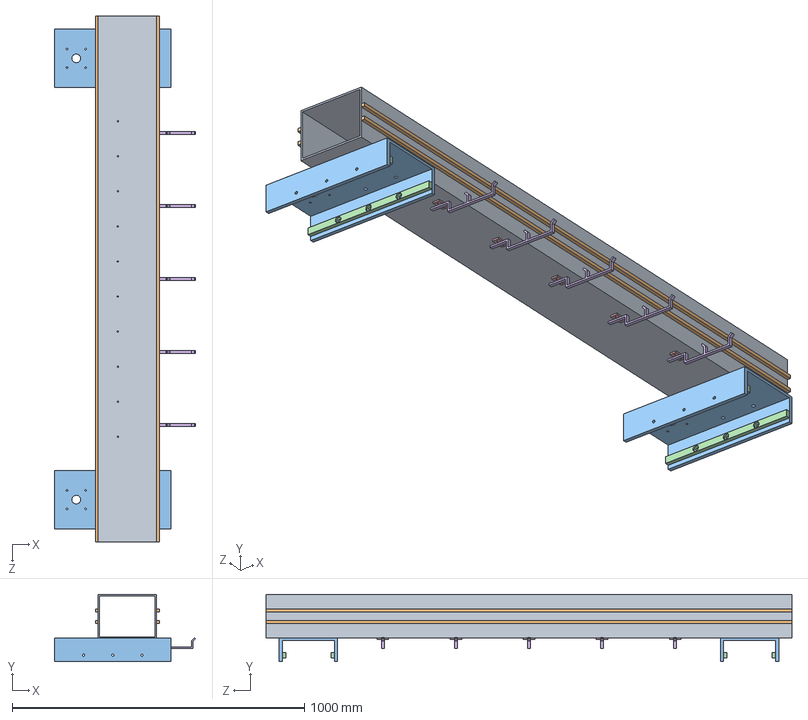
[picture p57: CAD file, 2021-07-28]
cad_files/PSP_BOT_CAD/Y_Assembly/Full_Y.SLDASM
483.5 x 230.0 x 1800.0 mm
Y_hollow_tube
Railings_y x 4
Slider_With_Roller x 2
UHMW_pad x 4
Bracket_Plate x 5
Drag_Chain_Bracket_Y x 5

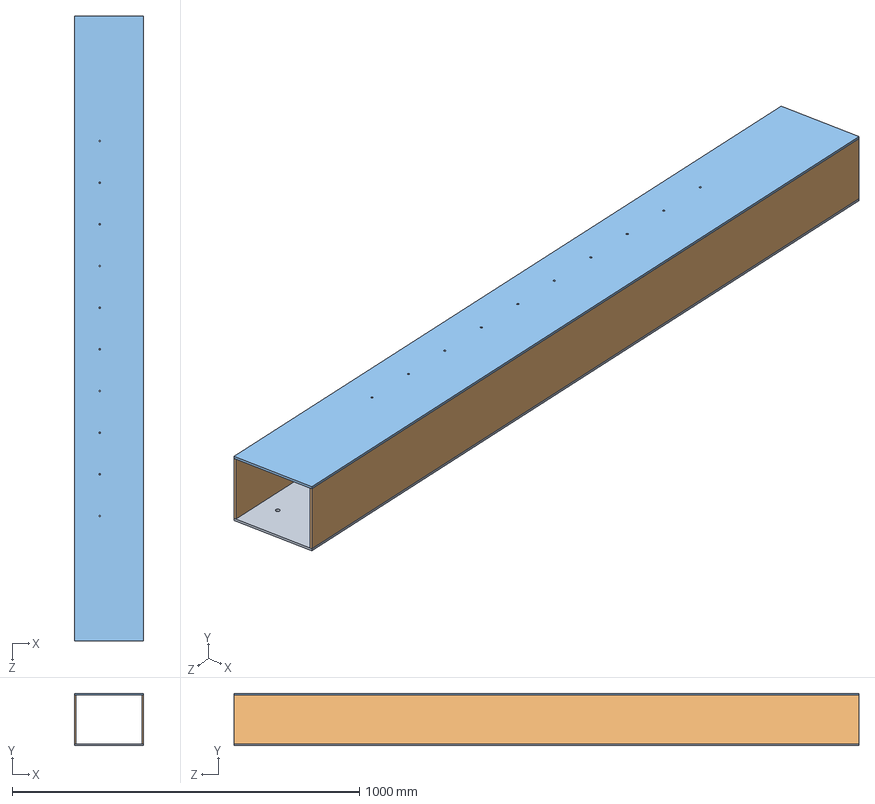
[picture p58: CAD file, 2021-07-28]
cad_files/PSP_BOT_CAD/Y_Assembly/Y_Tube/Y_Tube_Assem.SLDASM
200.0 x 150.0 x 1800.0 mm
Y_Plate_1
Y_Plate_2 x 2
Y_Plate_3

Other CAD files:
cad_files/Drag_Chain/MPSPS1520_50_57_S.sldasm
cad_files/DWG/Slider_Assembly.DWG
cad_files/PSP_BOT_CAD/Nesting/Nesting(10mm).SLDASM
cad_files/PSP_BOT_CAD/X_Assembly/X_Assembly.SLDASM
cad_files/Ball_Screw_Support/BSW8.sldasm
cad_files/Ball_Screw_Support/BSW8_3.sldprt
cad_files/Ball_Screw_Support/BSW8_5.sldprt
cad_files/Ball_Screw_Support/BSW8_8.sldprt
cad_files/DELTA_IA-ASM_200V_FRAME-F80H_BRAKE_3D_STP_EN_20150323/ECMA-CX0807SH.SLDPRT
cad_files/DELTA_IA-ASM_200V_FRAME-F80H_BRAKE_3D_STP_EN_20150323/ECMA-CX0807SH.stp
cad_files/DELTA_IA-ASM_200V_FRAME-F80_3D_STP_EN_20150323/ECMA-CX0804E7.stp
cad_files/DELTA_IA-ASM_200V_FRAME-F80_3D_STP_EN_20150323/ECMA-CX0807ES.stp
cad_files/DELTA_IA-ASM_200V_FRAME-F80_3D_STP_EN_20150323/ECMA-CX0807ES.stp.SLDPRT
cad_files/DWG/Ball_Screw.dwg
cad_files/DWG/Ball_Screw_Joint Drawing v1.dwg
cad_files/DWG/Ball_Screw_Joint.DWG
cad_files/DWG/Base_Plate_X.DWG
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

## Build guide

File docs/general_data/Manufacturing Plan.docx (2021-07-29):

Steps :

1) Welding between vertical column and supports

2) Fastening I rods with the plate above vertical column

3) screwing down rack on I rod

4) connecting the rollers on the slider plate and in turn connecting it to the I rod

5) I covering(plastic cap – clamp)

6) Welding Cuboid X on X Slider

7) welding cuboid Y on cuboid X

8) welding z base plate and z rod

9) Inserting the z rod on the y beam

10) welding y beam with cuboid Y

11) welding z cuboid on z rod

12) welding ball screw on z base plate

13) connecting ball screw and servo with the help of coupling

14) connecting gearbox and vertical arm rod with the help of coupling

15) welding between vertical arm rod and claw

Doubt :

1) base plate for rigid support

2) reducing the height of cuboid Y and increasing the length of Y Beam and then screwing y beam on cuboid Y

3) where to keep rollers for z rod motion, is it compulsory?

Parts :

Supports –

L shape(Steel) - complete solid structure

Rib(Steel) - would be welded to the L shaped brackets

Vertical Column(Steel) – Supports( L shape) will be welded to it

Rectangular Plate(Steel) – a plate of dimensions 300x208x20 mm , where 4 holes will be drilled at corners.

X Part :

I rod(Aluminium) –Will be fastened using screws on the rectangular plate

X Pinion (Mild steel) – Module-1.75, teeths- 20, shaft hole - (To be determined)

X Rack(Mild steel) - Module -1.75, length-1500mm, it will be screwed down to the I beam via 5 Flathead screws at equal intervals

X Rollers(Steel) –

X Sliders( – plate - an aluminium plate of dimensions 350x164x15mm with 4 corners holes where the rollers will be screwed down and also a centre hole for the shaft to be mounted.

Cuboid_X (Aluminium) – Solid cuboid welded to the Y beam, and connects the beam with the X slider plate.

Y Part :

Cuboid_Y –

Y Beam(aluminium) – A beam of length 1100mm and a hollow cross section of 180x130mm welded to the cuboid on which we will place the Z Vertical slider

Y Rack (mild steel) - Module -1.75, length-1100mm, it will be screwed down to the I beam via 5 Flathead screws at equal intervals

Y Pinion (mild steel)– Module-1.75, teeths- 20, shaft hole - (To be determined)

Y rollers (steel) – Probably cylindrical Rollers connected to Z Vertical Slider with Screws

Z Part :

Z base plate (aluminium) –Welded to the bottom of the Z vertical slider, providing the ball screw support

Z rod (aluminium) –

Cuboid_Z (Vertical slider) (Aluminium) – placing along the beam, house the servo and gear box on an extended plate and also the rollers. A servo is mounted on the top for the Motion in Z axis of the arm via ball screw. Internally hollow structure.

Z Rollers – Cylindrical rollers connected to the Z_L shape

Z_L shape (Aluminium) – L shaped Bracket connected to the ball screw via a Nut housing connected to it

Z ball screw (Mild Steel) – Ball screw of length 608mm connected to a servo at one end and connected to the Base plate at the other end, should be rotatable.

Vertical arm – connected to a coupling(which will be present above the L shaped plate

Claw – welded to the vertical arm

Vertical column -> X _I beam -> X Rack and pinion -> X_Slider plate with rollers and servos ->

X_Cuboid -> Y_Cuboid -> Y_Beam -> Y_Rack and Pinion -> Z_cuboid with Z base plate ->

Servos for Y axis motion and rollers -> Servos for Z_axis motion -> Z_Ball Screw -> Z_L_shape

connected to the nut -> Servos for Z axis rotation -> Gripper

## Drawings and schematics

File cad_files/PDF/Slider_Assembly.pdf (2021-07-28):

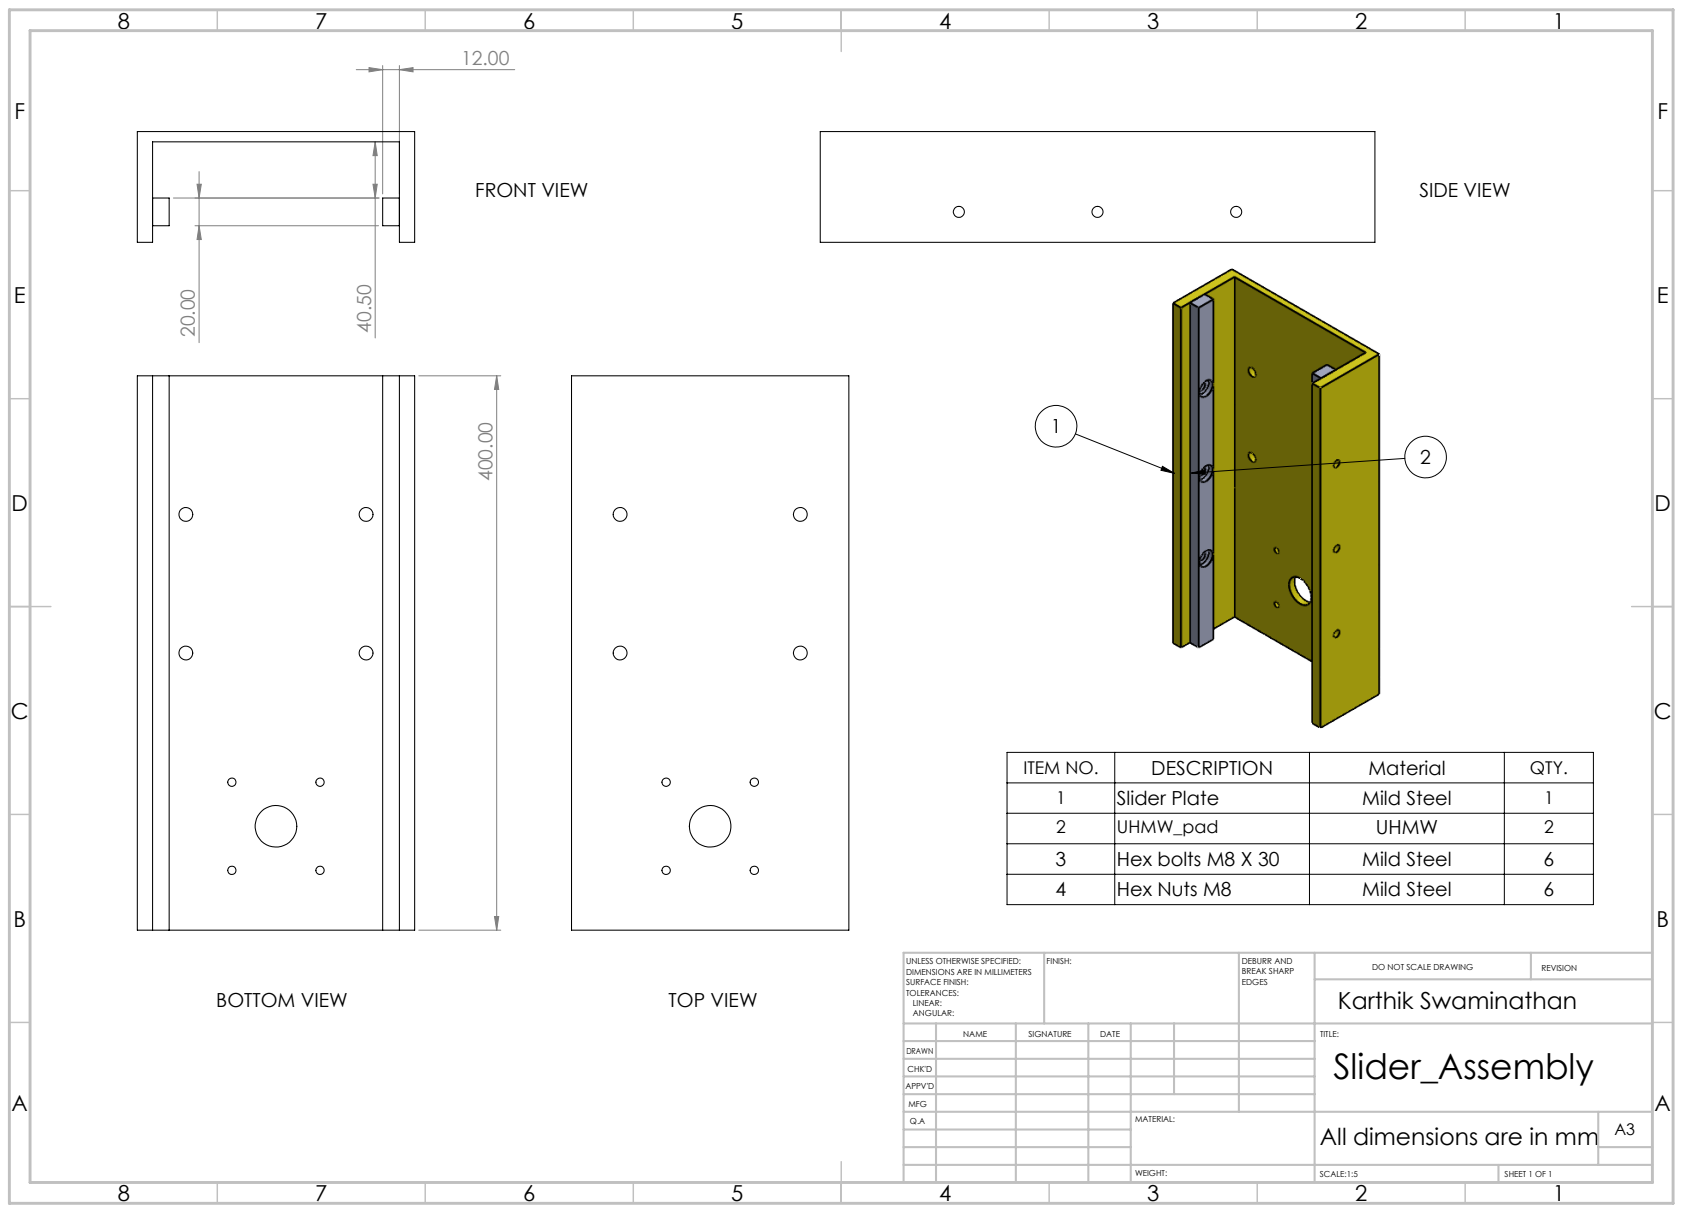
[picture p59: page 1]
FRONT VIEW; SIDE VIEW; BOTTOM VIEW; TOP VIEW; FINISH:; DEBURR AND; BREAK SHARP; DO NOT SCALE DRAWING; REVISION; SCALE:1:5; SHEET 1 OF 1; Karthik Swaminathan

ITEM NO. | DESCRIPTION | Material | QTY.
1 | Slider Plate | Mild Steel | 1

3 | Hex bolts M8 X 30 | Mild Steel | 6
4 | Hex Nuts M8 | Mild Steel | 6

UNLESS OTHERWISE SPECIFIED:
DIMENSIONS ARE IN MILLIMETERS
SURFACE FINISH:
TOLERANCES:
LINEAR:
ANGULAR:

NAME | SIGNATURE | DATE | | | | TITLE: Slider_Assembly

DRAWN
CHK'D
APPV'D
MFG
Q.A | | | | MATERIAL: | All dimensions are in mm | A3

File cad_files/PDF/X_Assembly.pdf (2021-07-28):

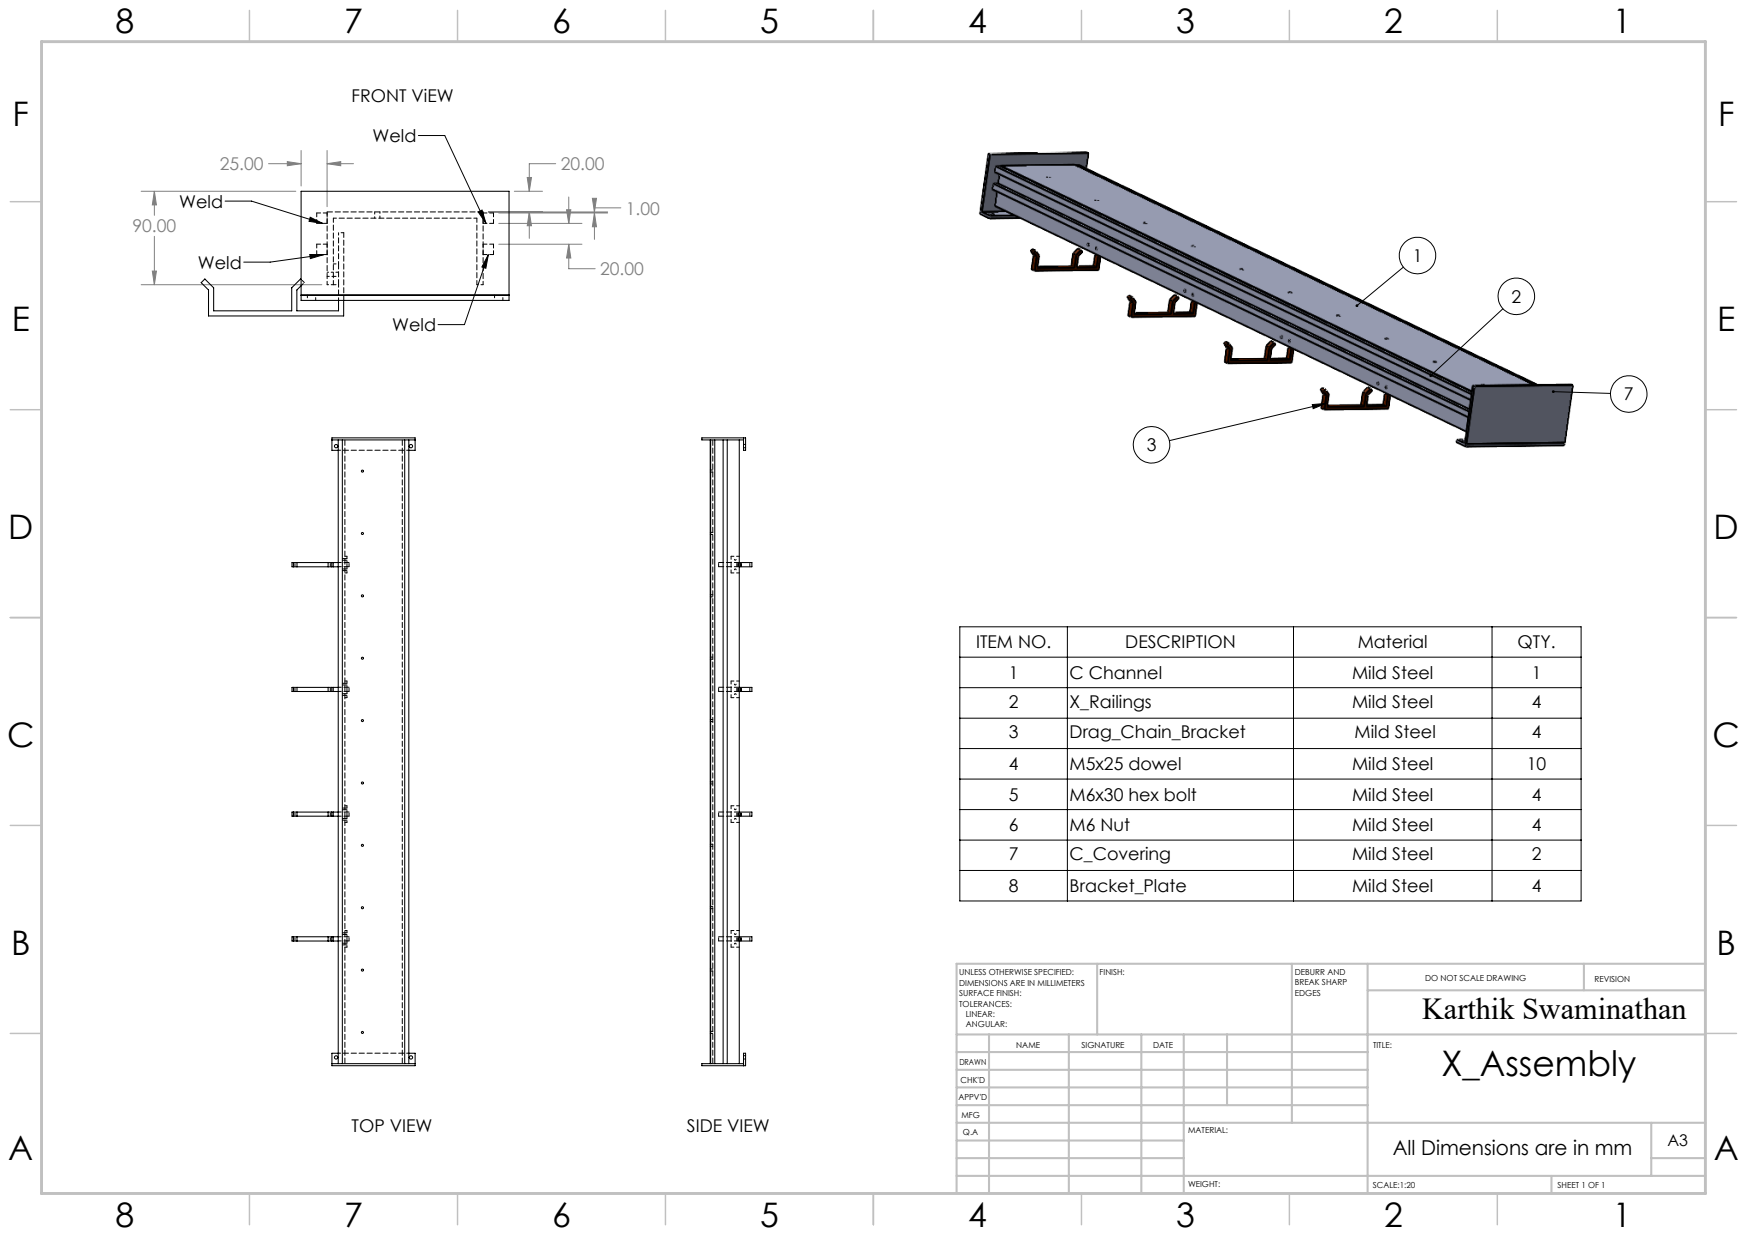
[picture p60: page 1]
FRONT ViEW; TOP VIEW; SIDE VIEW; FINISH:; DEBURR AND; BREAK SHARP; DO NOT SCALE DRAWING; REVISION; SCALE:1:20; SHEET 1 OF 1; Karthik Swaminathan

ITEM NO. | DESCRIPTION | Material | QTY.
1 | C Channel | Mild Steel | 1
2 | X_Railings | Mild Steel | 4
3 | Drag_Chain_Bracket | Mild Steel | 4
4 | M5x25 dowel | Mild Steel | 10
5 | M6x30 hex bolt | Mild Steel | 4
6 | M6 Nut | Mild Steel | 4
7 | C_Covering | Mild Steel | 2
8 | Bracket_Plate | Mild Steel | 4

UNLESS OTHERWISE SPECIFIED:
DIMENSIONS ARE IN MILLIMETERS
SURFACE FINISH:
TOLERANCES:
LINEAR:
ANGULAR:

NAME | SIGNATURE | DATE | | | | TITLE: X_Assembly

DRAWN
CHK'D
APPV'D
MFG
Q.A | | | | MATERIAL: | All Dimensions are in mm | A3

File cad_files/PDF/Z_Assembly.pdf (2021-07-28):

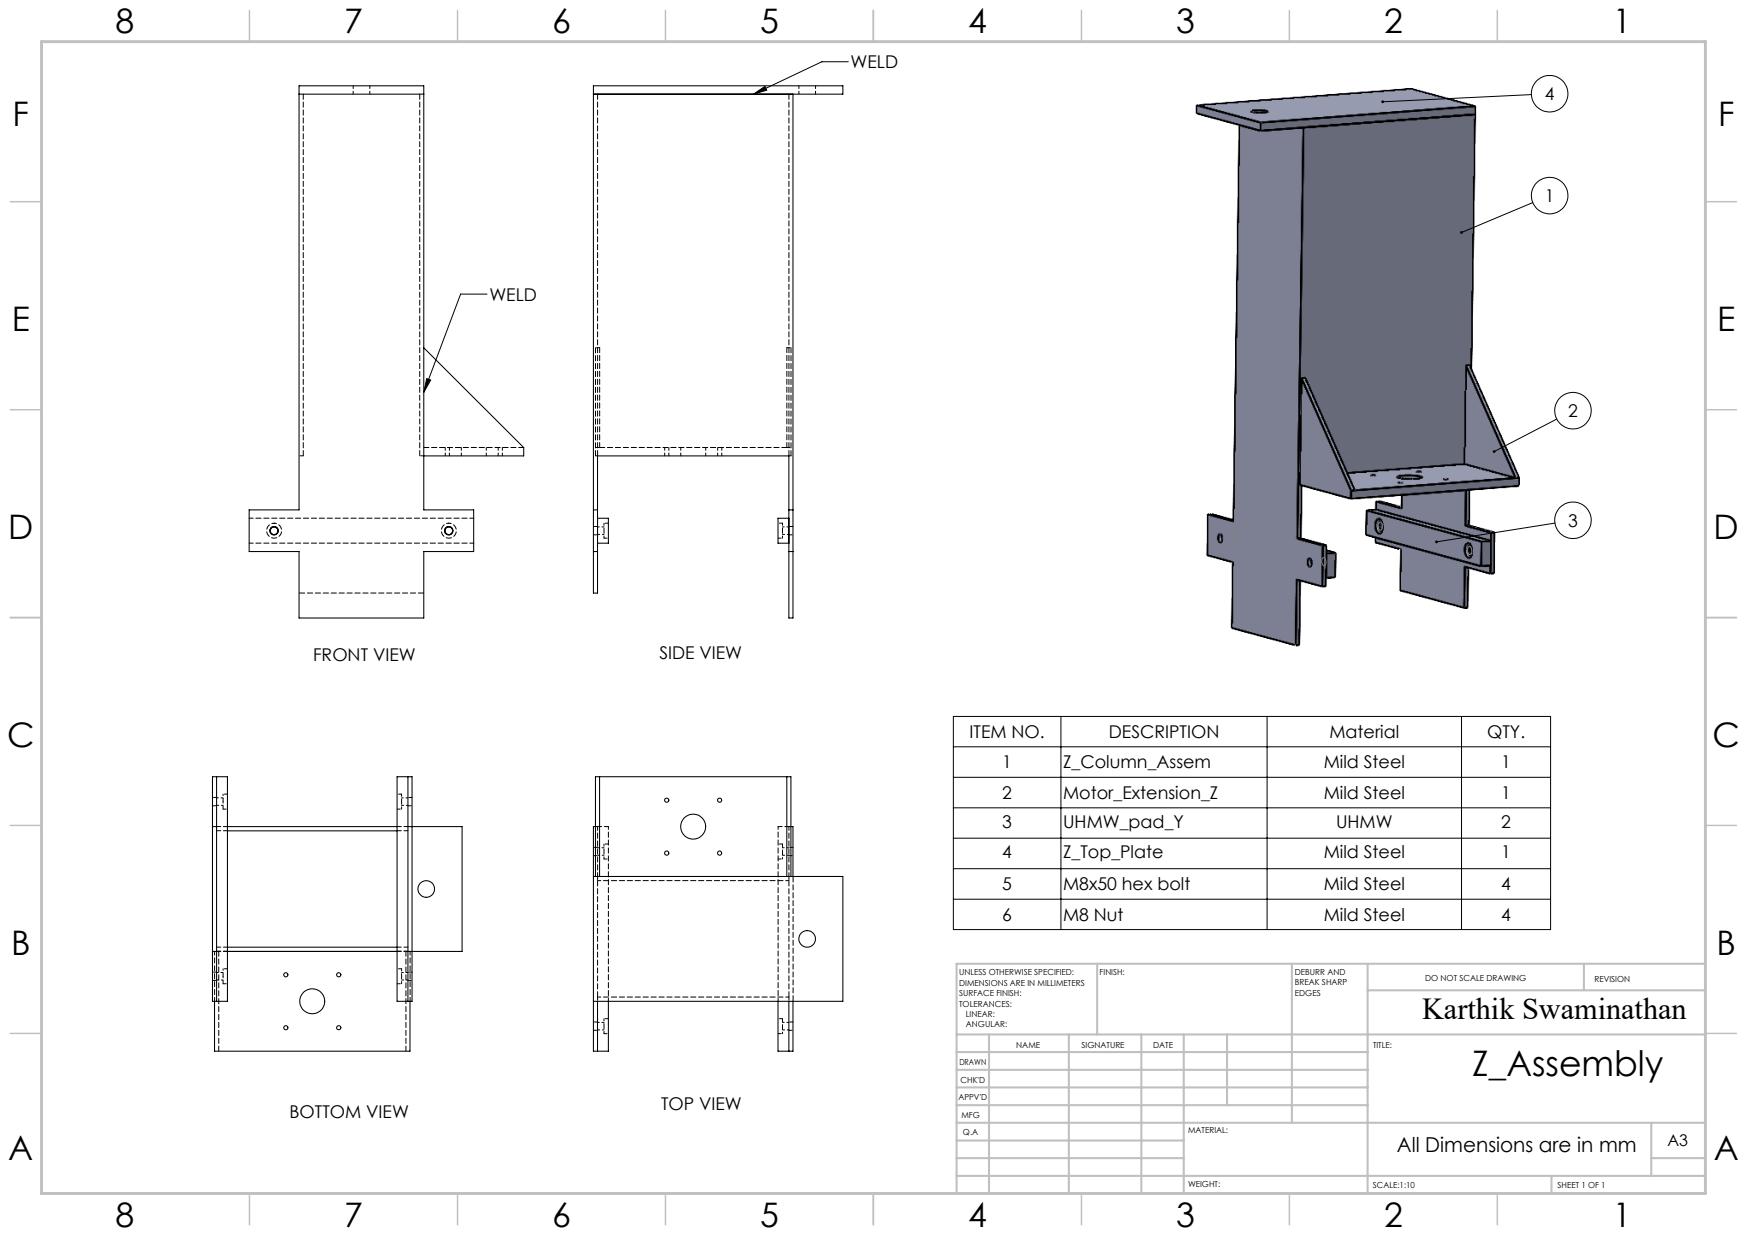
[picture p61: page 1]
SIDE VIEW; TOP VIEW; FRONT VIEW; BOTTOM VIEW; FINISH:; DEBURR AND; BREAK SHARP; DO NOT SCALE DRAWING; REVISION; SCALE:1:10; SHEET 1 OF 1; Karthik Swaminathan

ITEM NO. | DESCRIPTION | Material | QTY.
1 | Z_Column_Assem | Mild Steel | 1
2 | Motor_Extension_Z | Mild Steel | 1
3 | UHMW_pad_Y | UHMW | 2
4 | Z_Top_Plate | Mild Steel | 1
5 | M8x50 hex bolt | Mild Steel | 4
6 | M8 Nut | Mild Steel | 4

UNLESS OTHERWISE SPECIFIED:
DIMENSIONS ARE IN MILLIMETERS
SURFACE FINISH:
TOLERANCES:
LINEAR:
ANGULAR:

NAME | SIGNATURE | DATE | | | | TITLE: Z_Assembly

DRAWN
CHK'D
APPV'D
MFG
Q.A | | | | MATERIAL: | All Dimensions are in mm | A3

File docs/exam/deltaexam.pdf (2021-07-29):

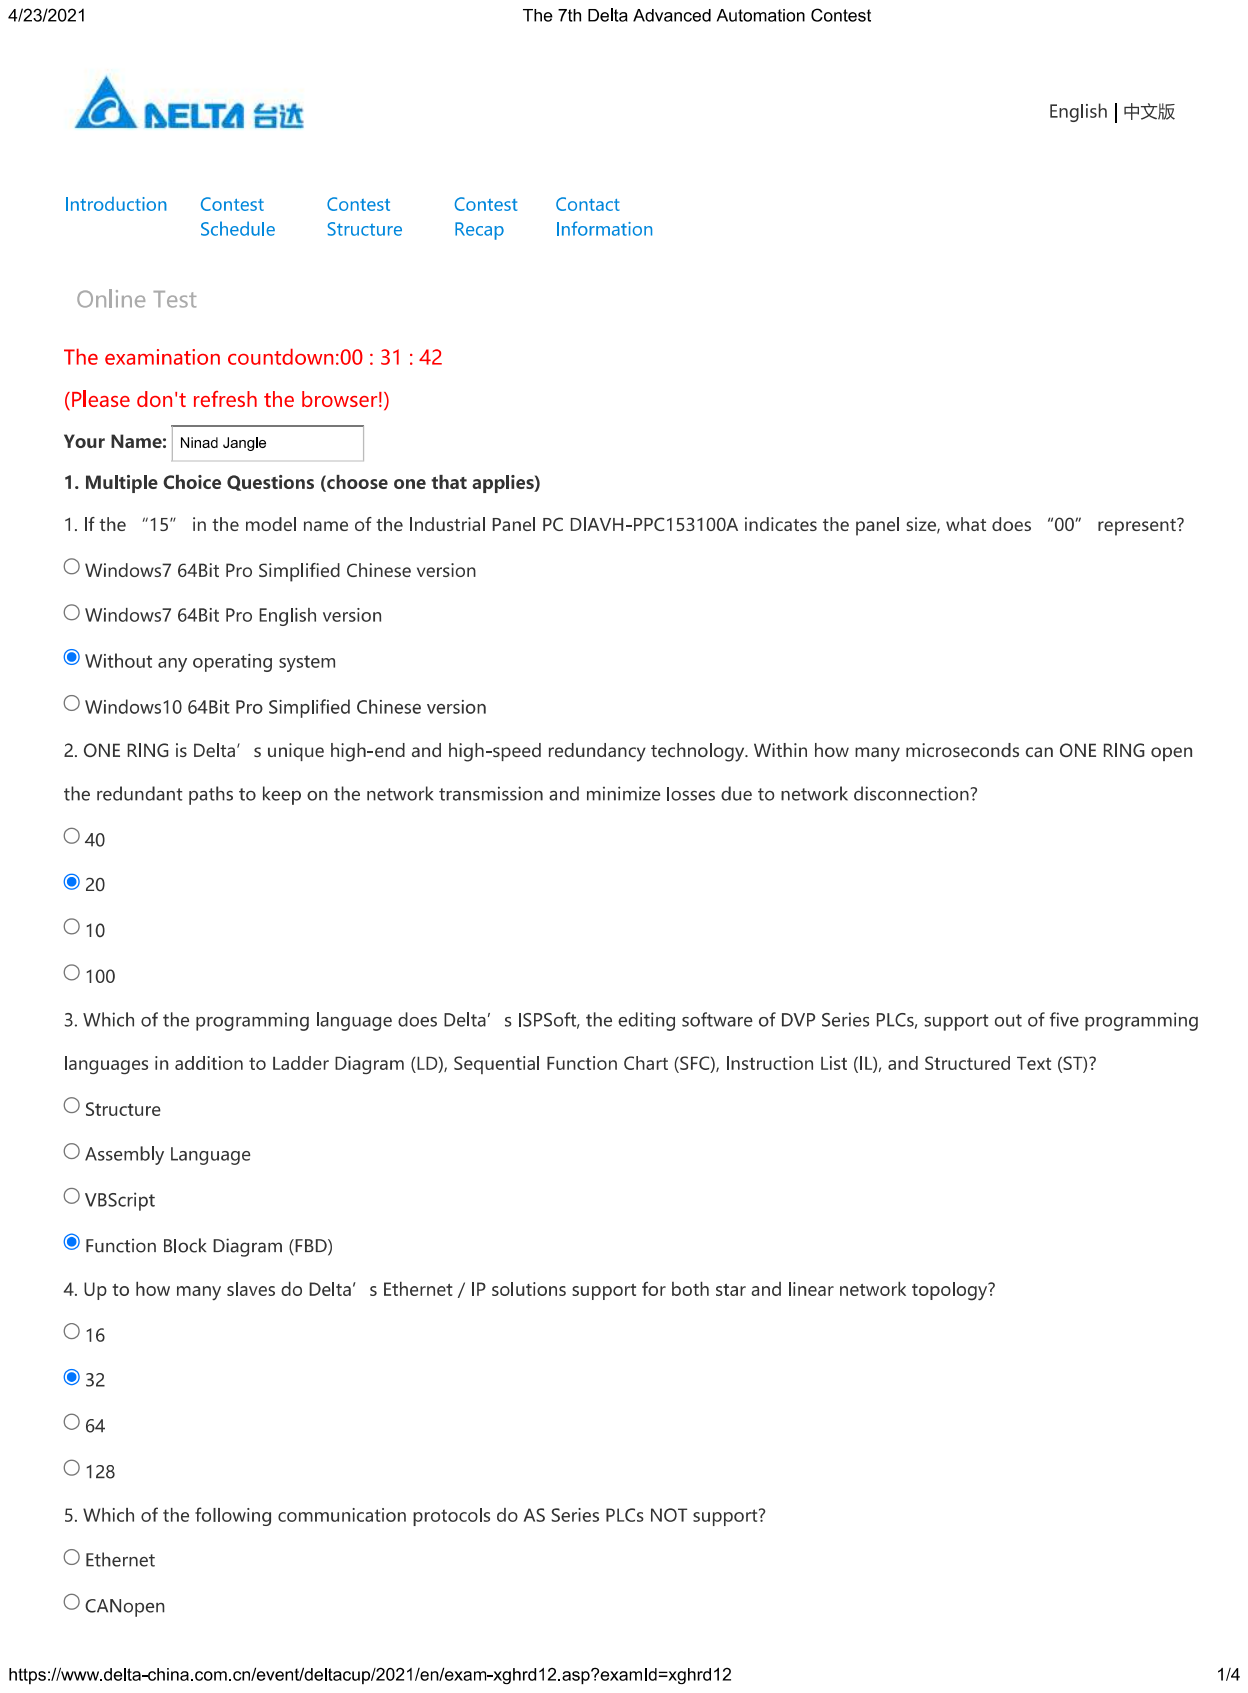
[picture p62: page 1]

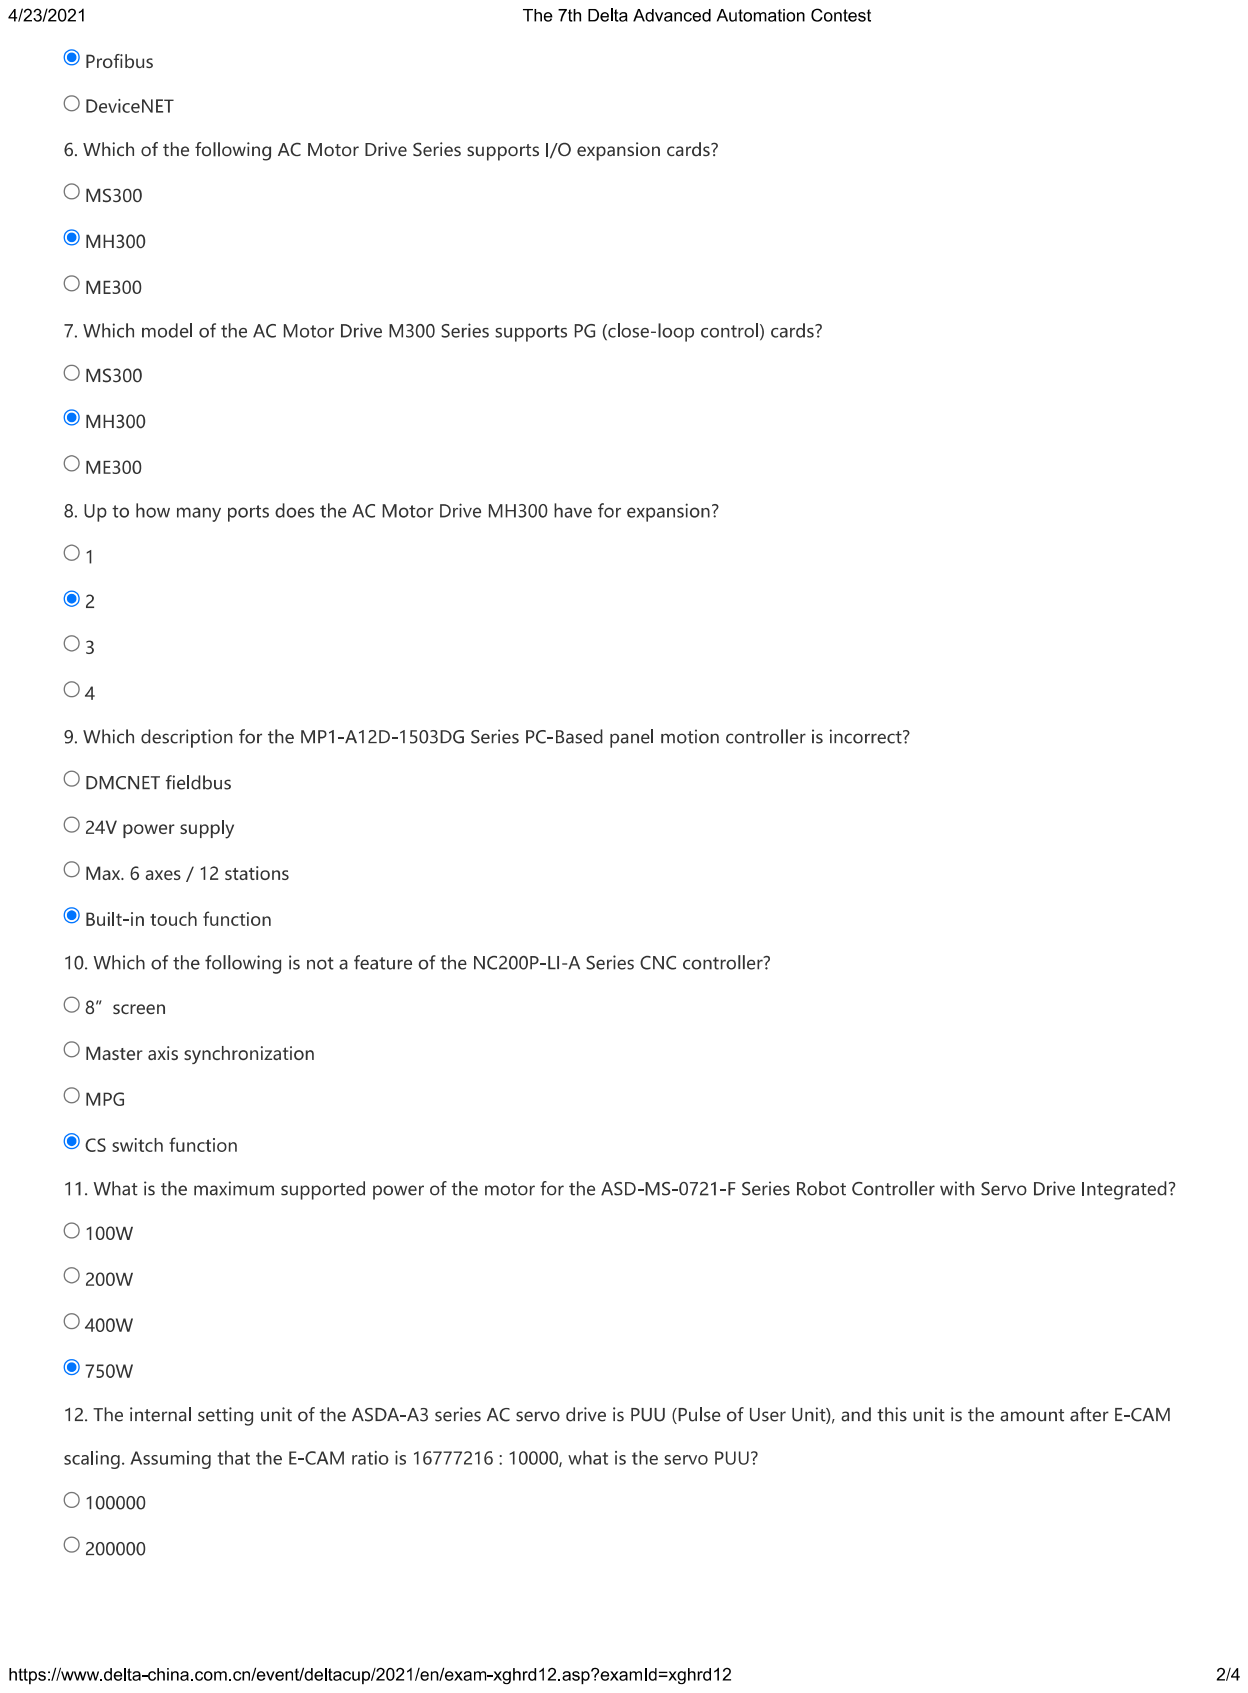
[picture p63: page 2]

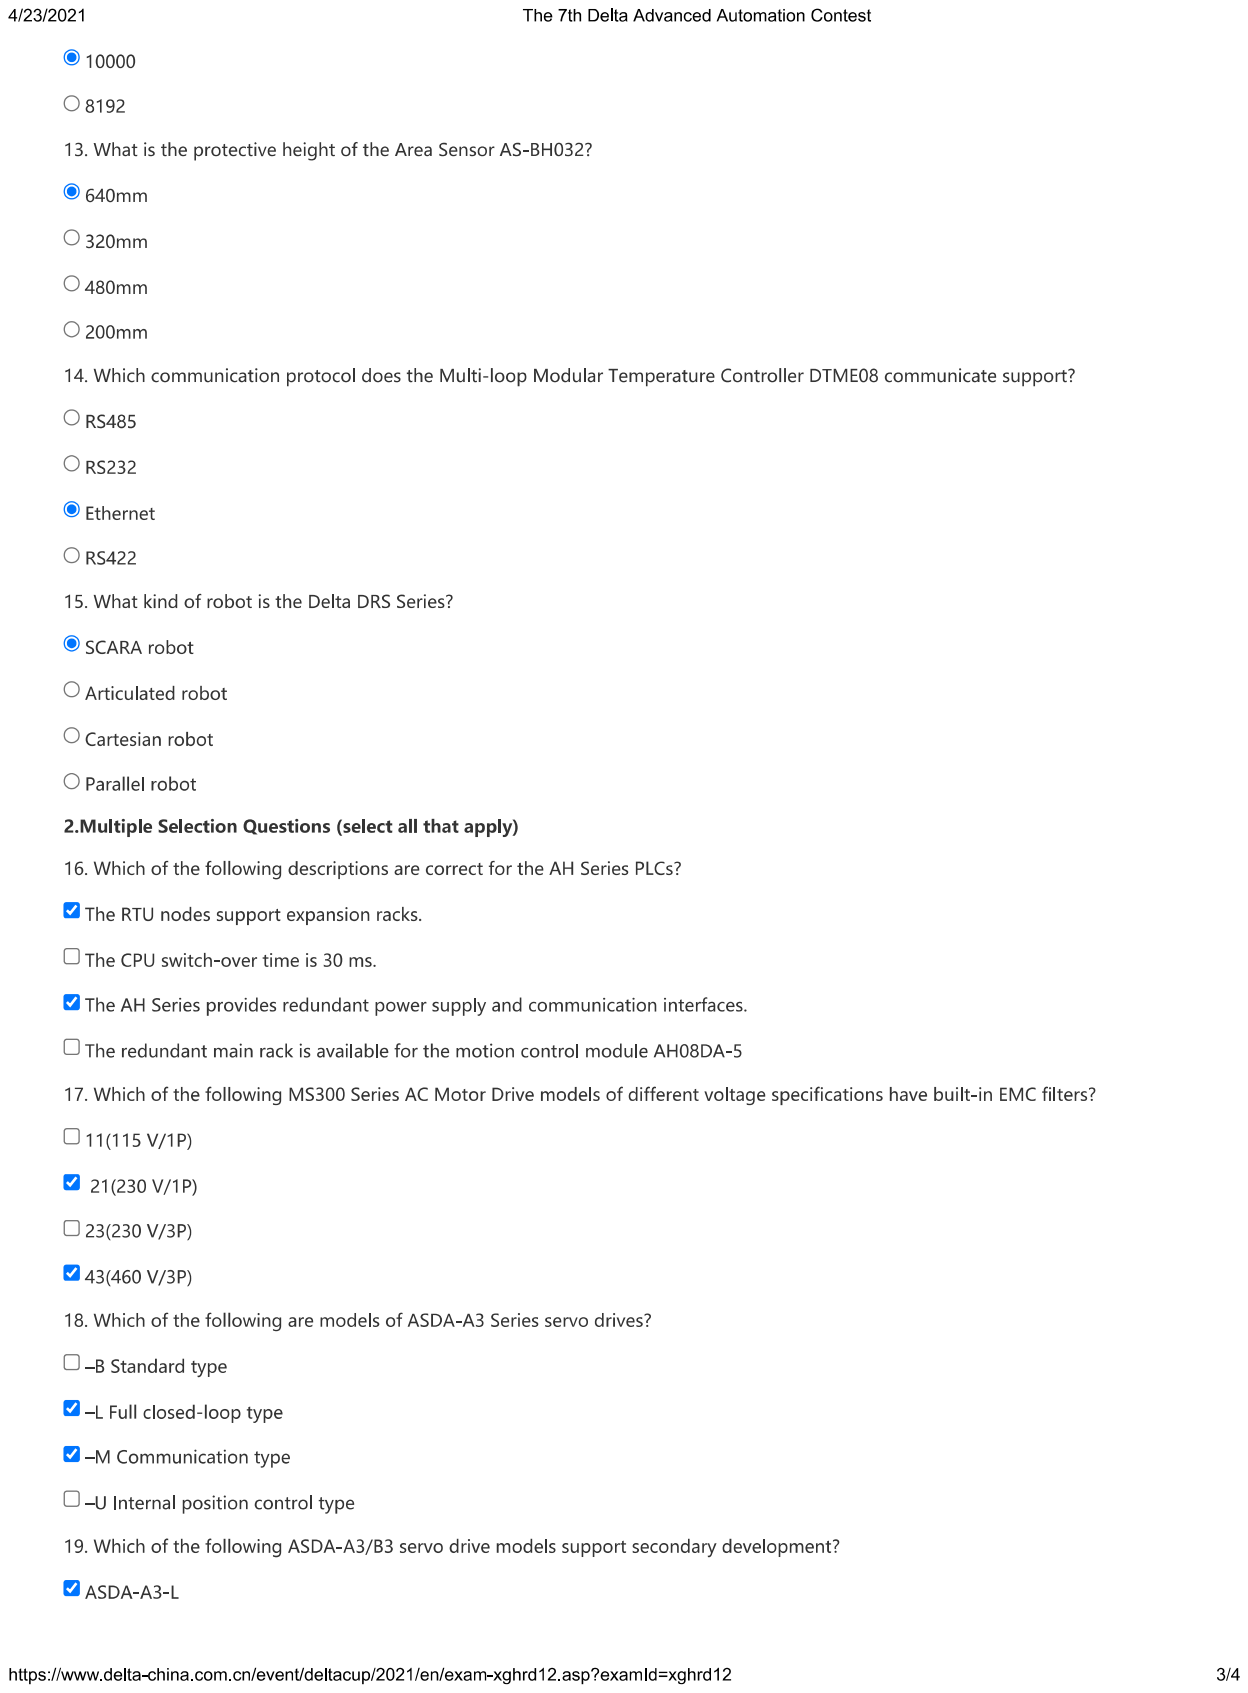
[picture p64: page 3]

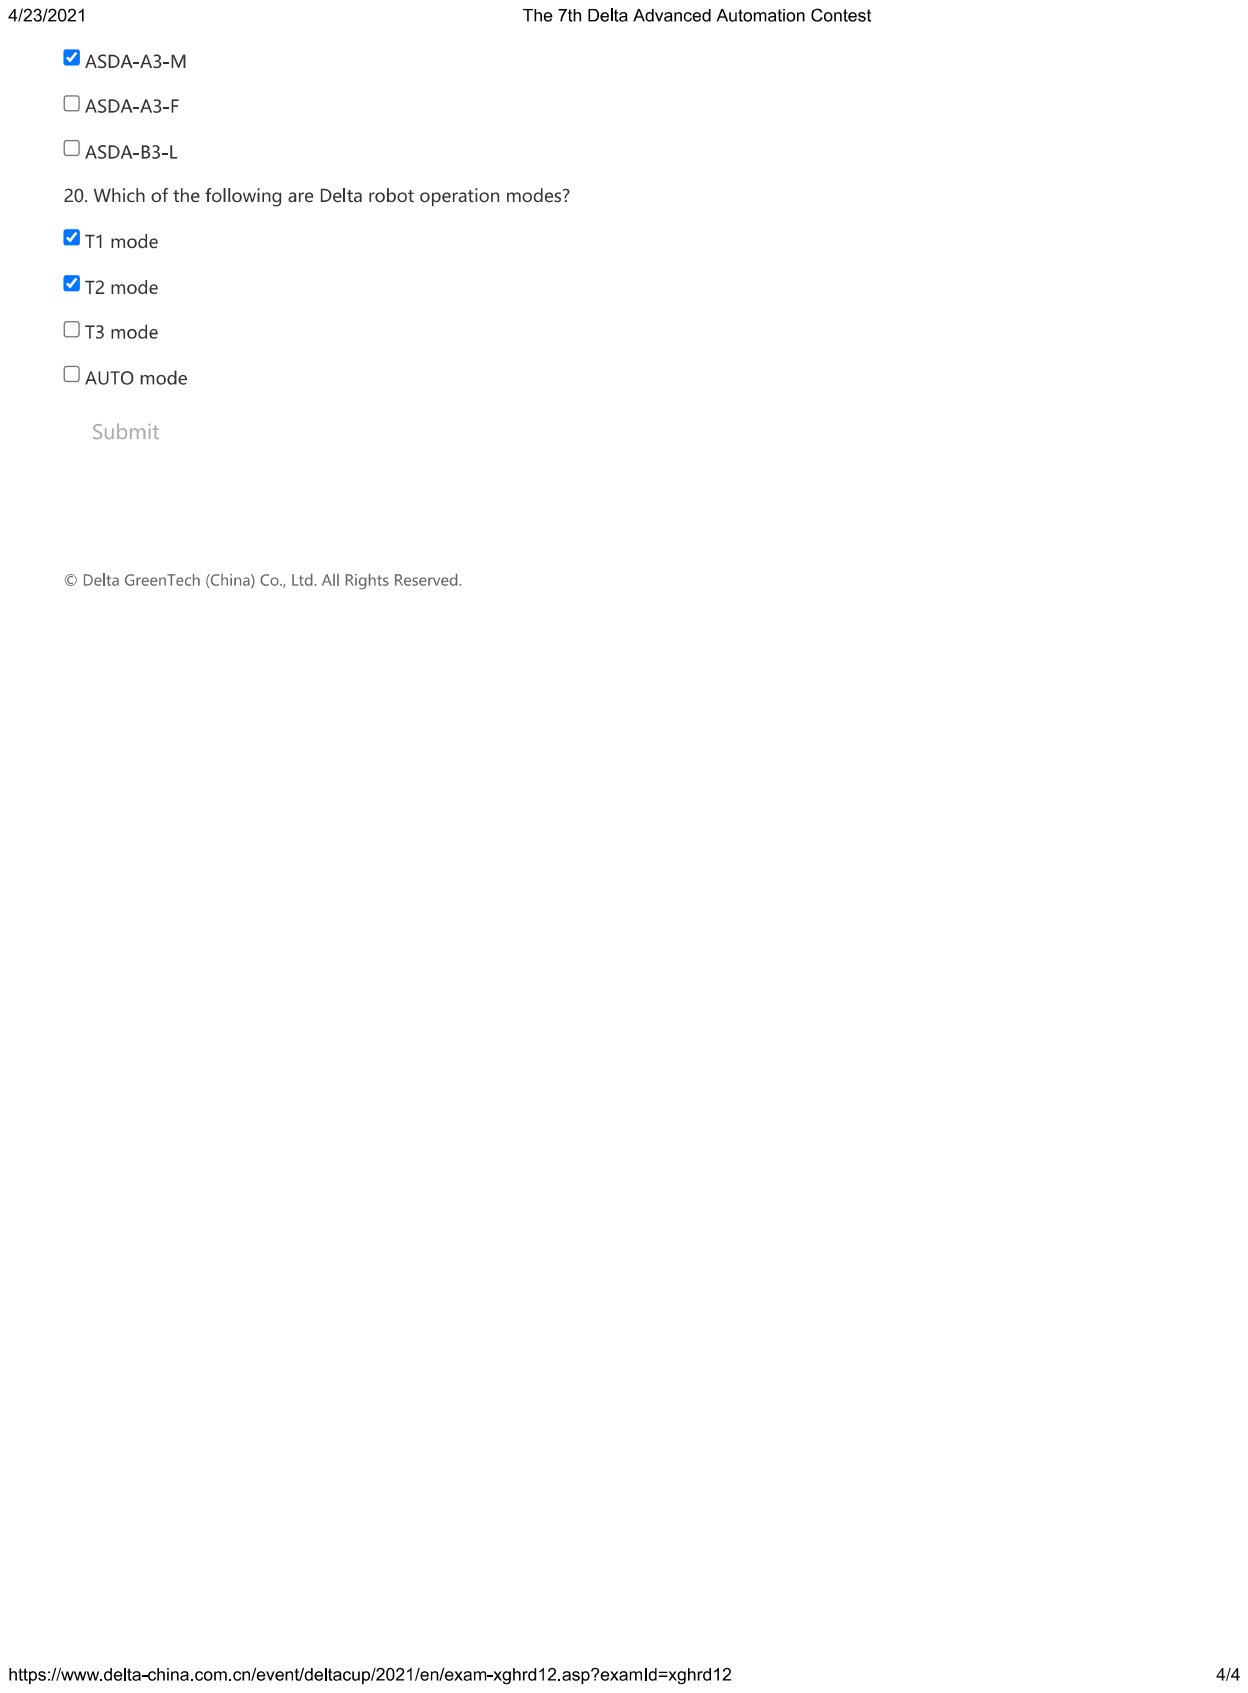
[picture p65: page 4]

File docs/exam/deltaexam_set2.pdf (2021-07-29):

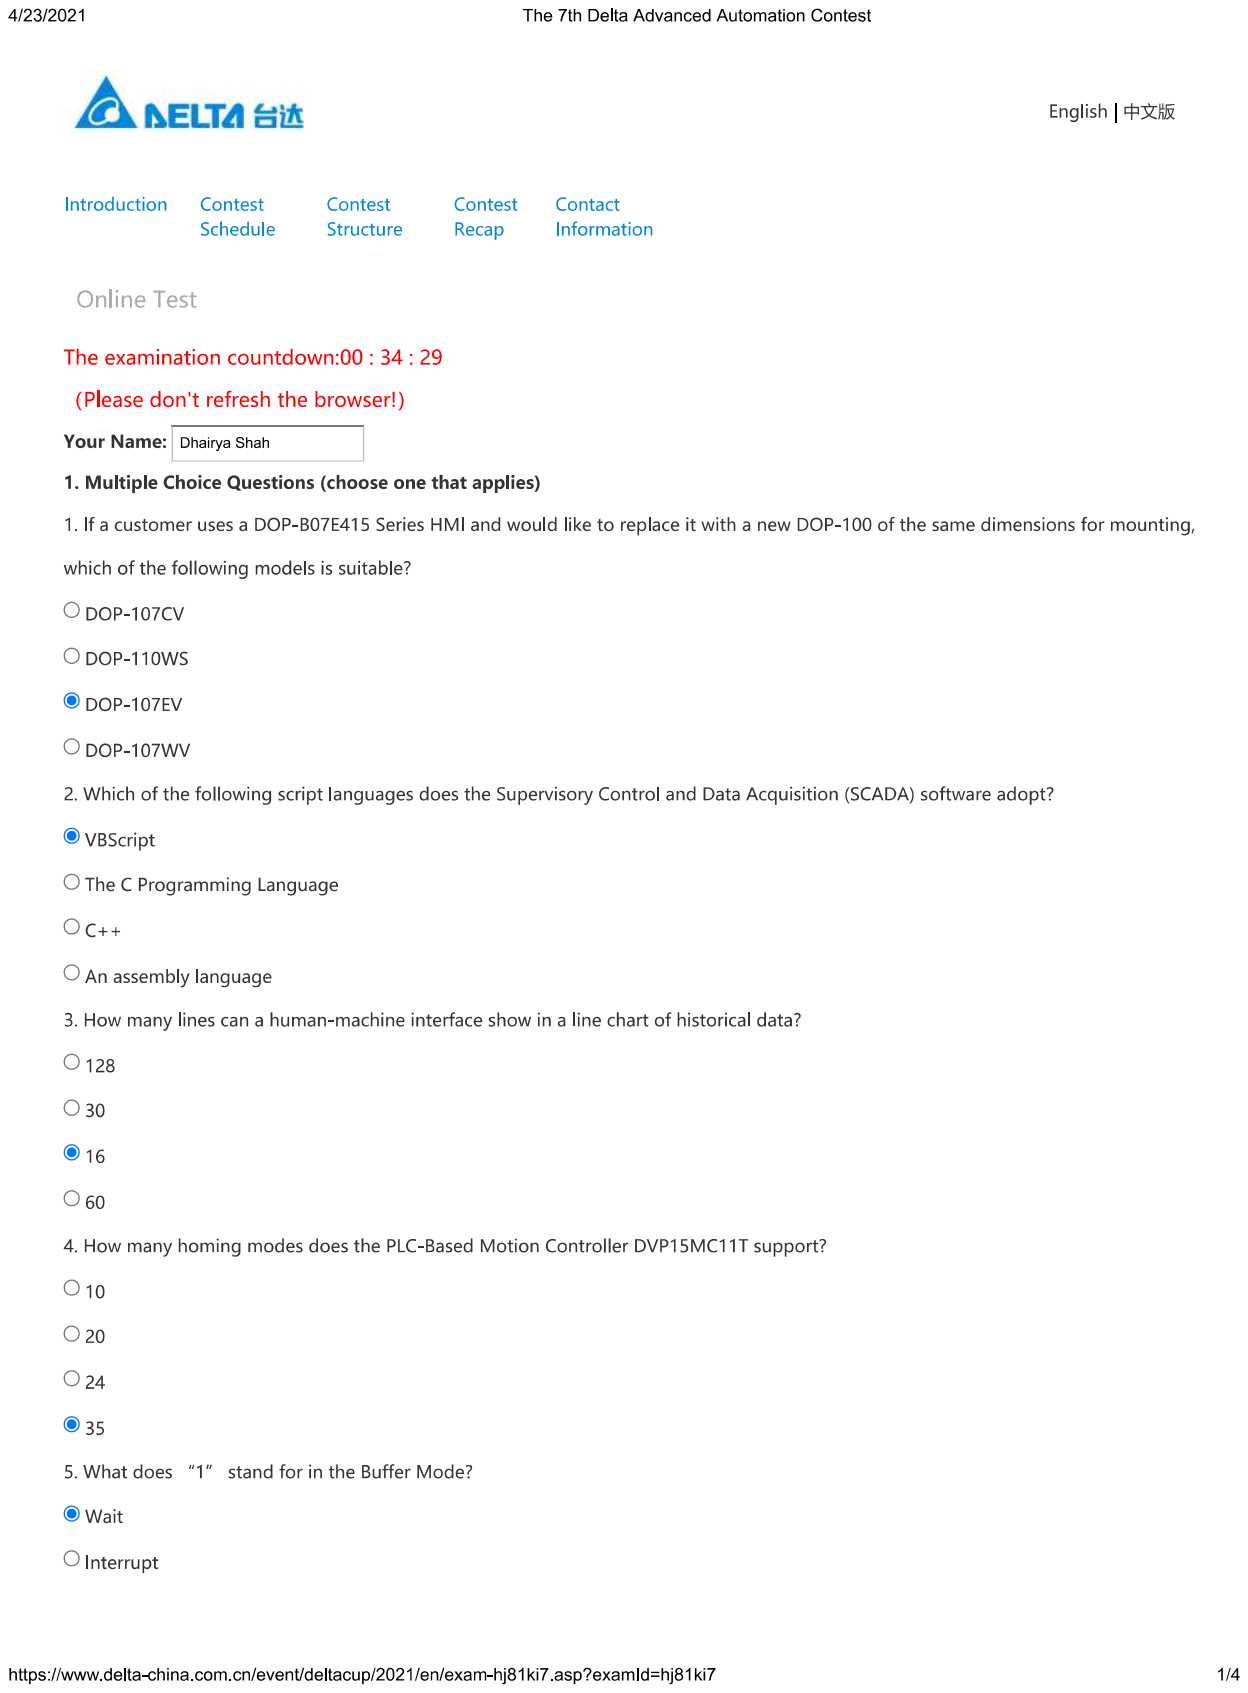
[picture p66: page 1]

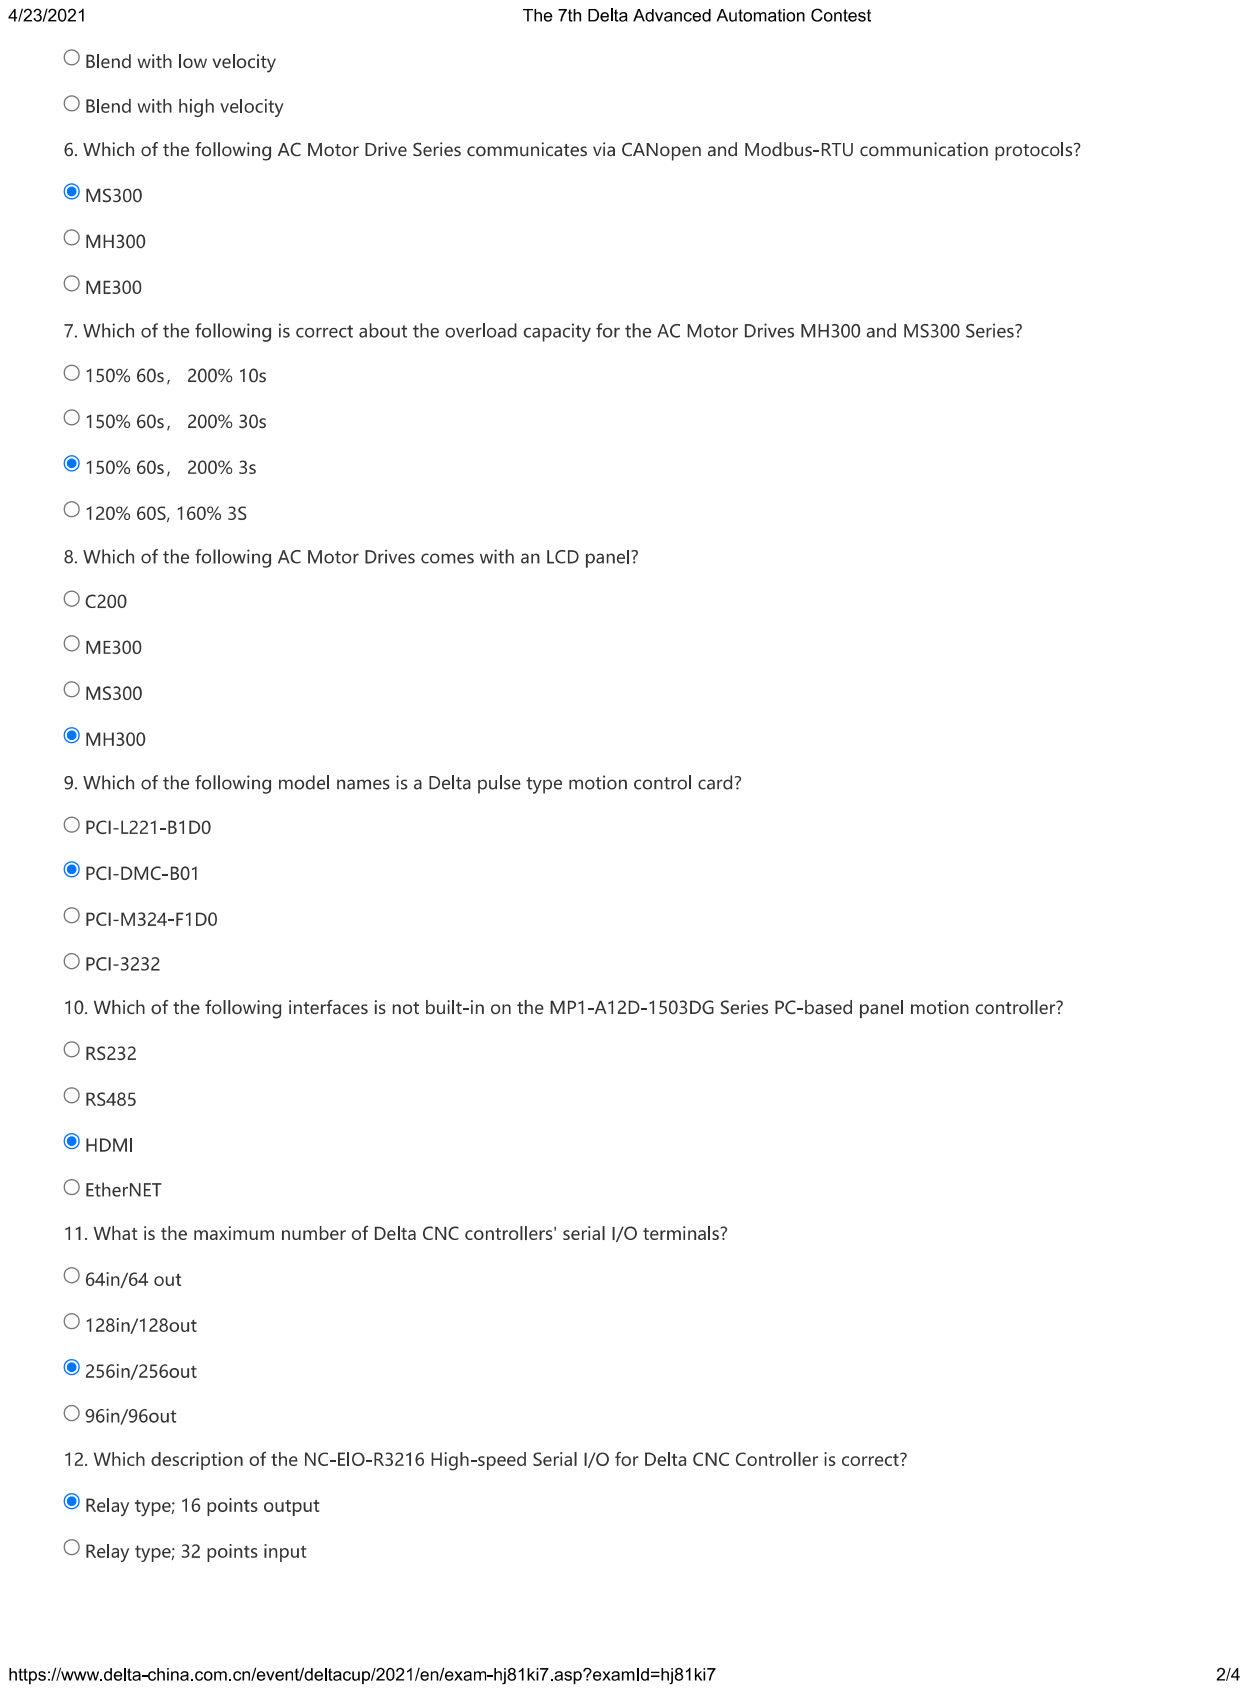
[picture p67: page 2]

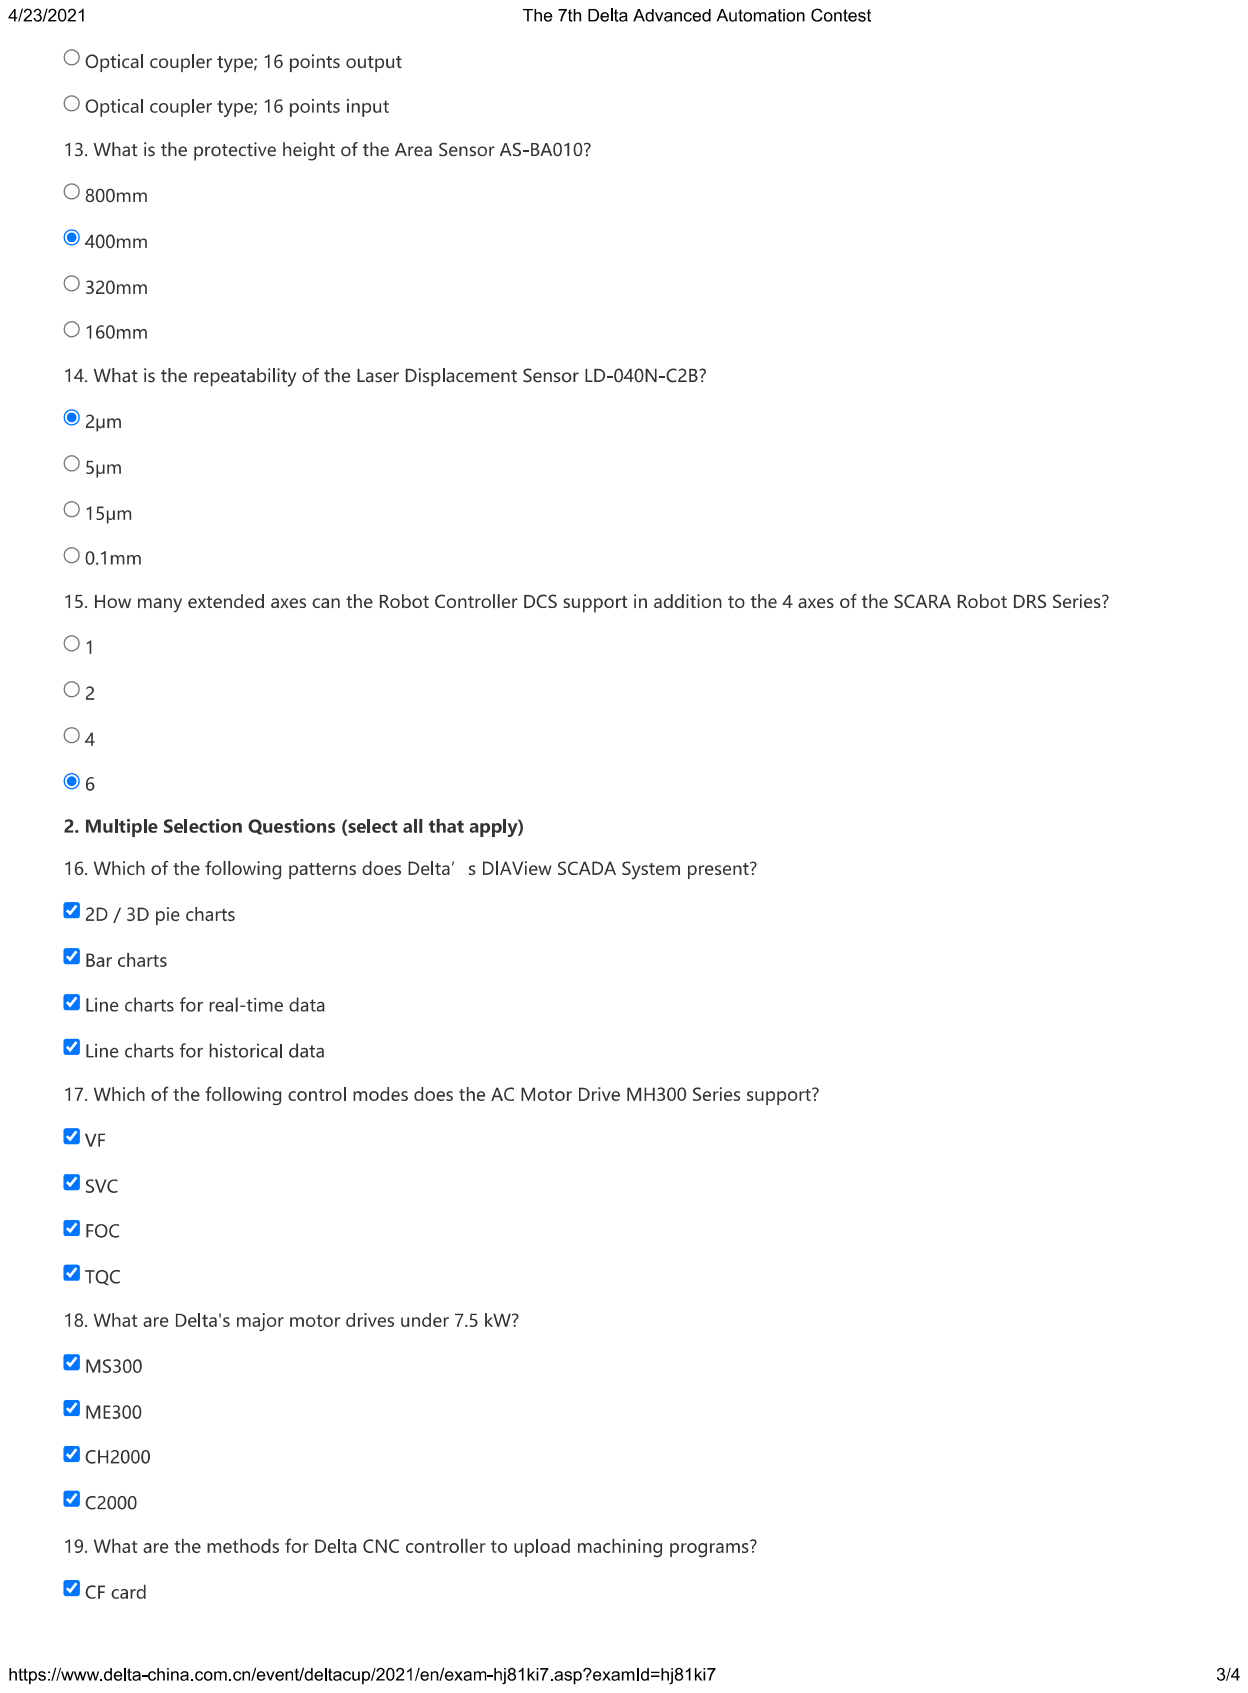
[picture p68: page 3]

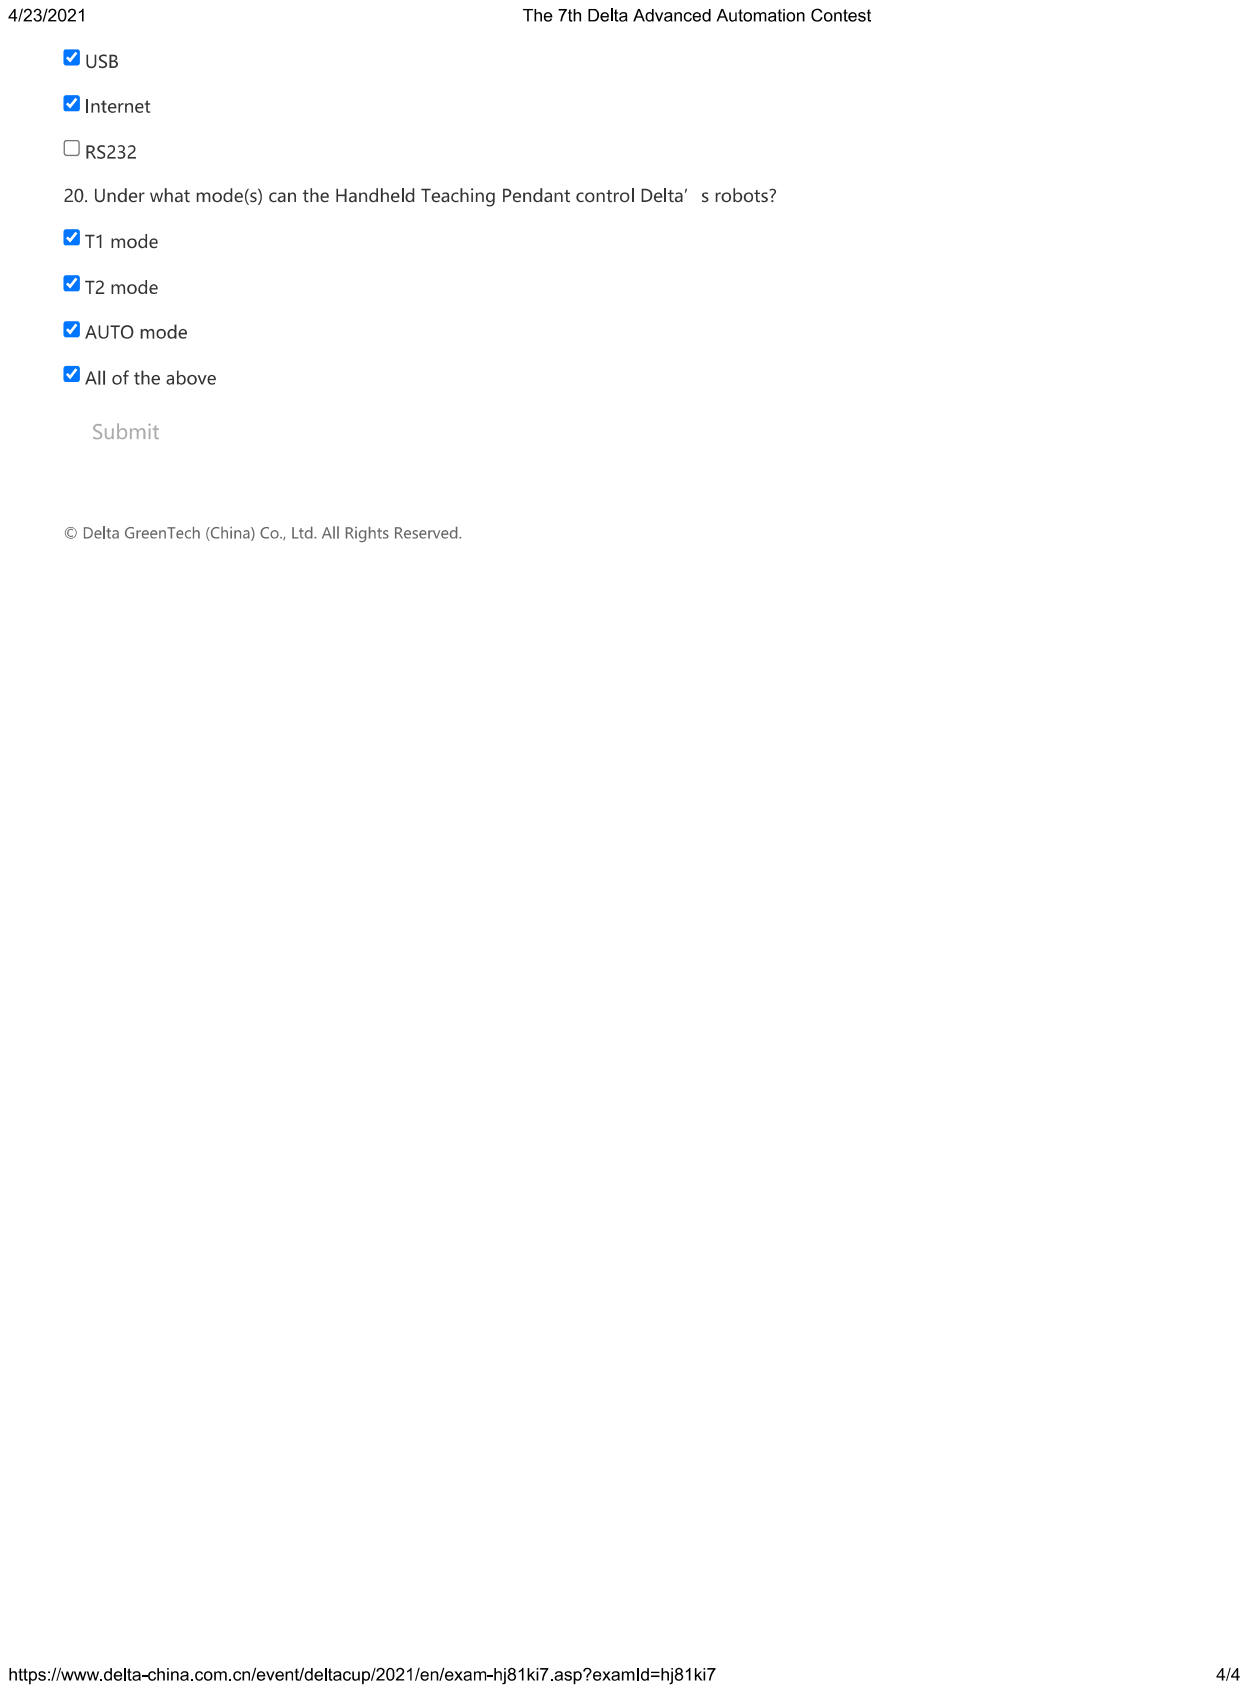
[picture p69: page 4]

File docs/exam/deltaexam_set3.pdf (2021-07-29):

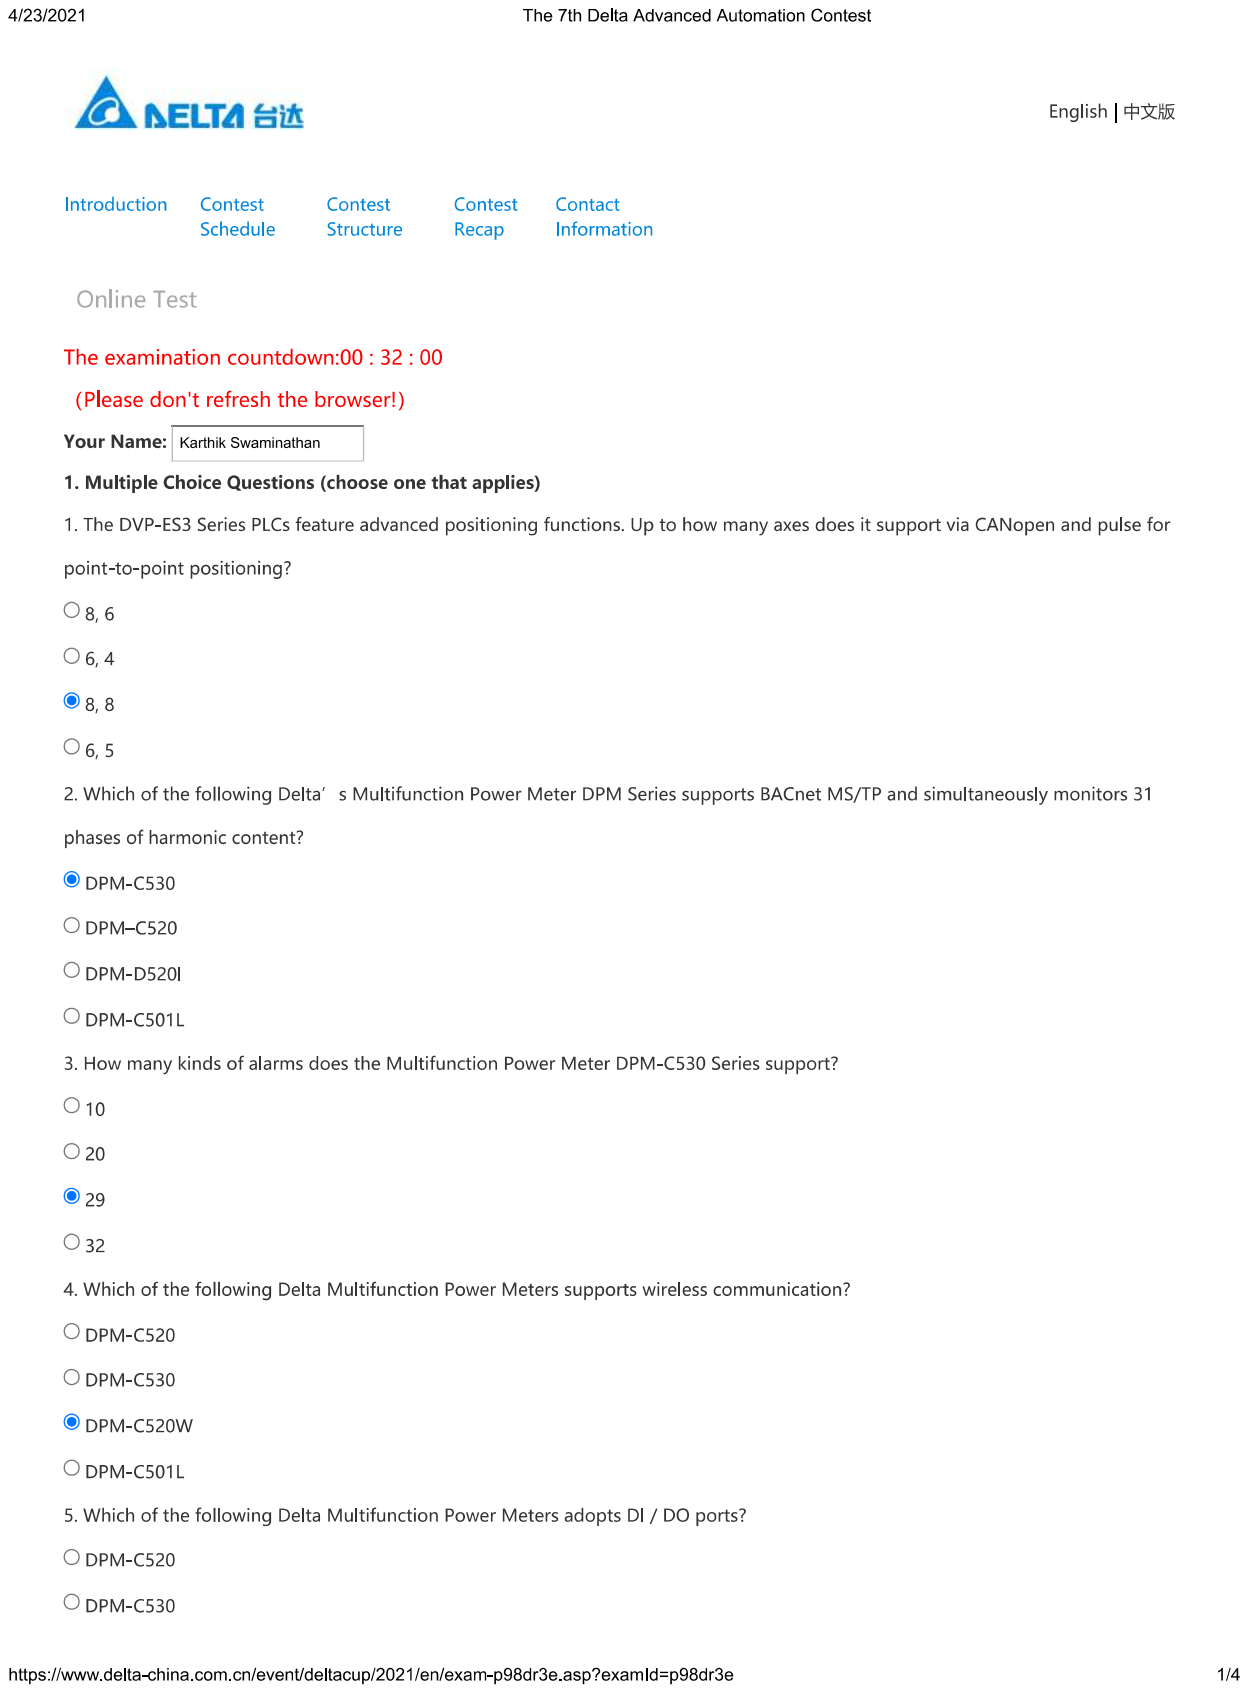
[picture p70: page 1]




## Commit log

2021-07-28 PSP Bot CAD Files
    [BSW8.sldasm, BSW8_3.sldprt, BSW8_5.sldprt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]
2021-07-29 Changes folder name
    [BSW8.sldasm, BSW8_3.sldprt, BSW8_5.sldprt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]
2021-07-29 Added datasheets and assets
    [BSW8.sldasm, BSW8_3.sldprt, BSW8_5.sldprt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]
